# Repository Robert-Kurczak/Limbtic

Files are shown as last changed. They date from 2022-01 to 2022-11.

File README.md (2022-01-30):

# Limbtic
Project Limbtic is an attempt to build a robotic arm that you can control using you own hand. Robotic arm can be bigger, stronger, more precise,
creating many application possibilities.

## Table of Contents
* [General info](#general-info)
* [Hardware](#hardware)

## General info
This project is currently more hardware focused, as I am working on circuit that can handle reading a lot of analog sensors, transform reading into binary form and
send it further so the data can be appropriately proccesed. This circuit have to be fast, precise and noise-resistant.
This kind of circuit have potential on its own as it can be used for example as VR hand controller.

## Hardware
### Sensor Reader
##### Schematic
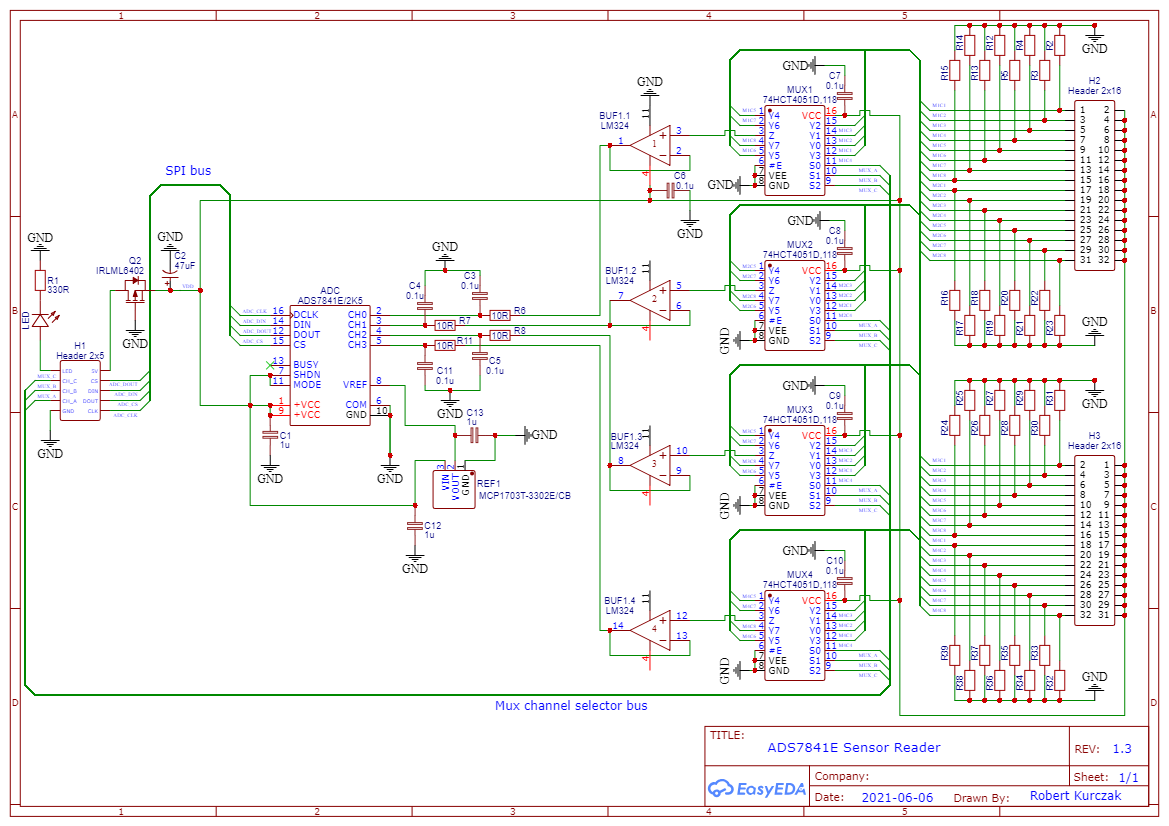
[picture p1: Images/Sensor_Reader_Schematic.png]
Sensor Reader Schematic

##### PCB project
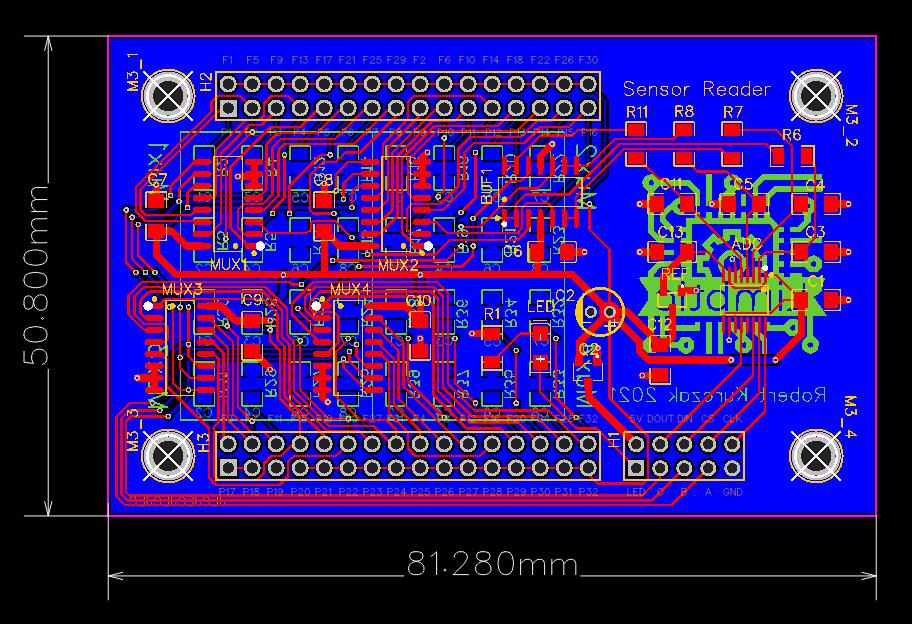
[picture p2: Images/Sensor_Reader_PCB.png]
Sensor Reader PCB project

##### Real photo
Sensor Reader Photo

#### How does it work?
I want to read arm joints angles using some flexible pressure sensors as they're far cheaper than bend sensors, and can be cut to different sizes.
The more you bend sensor, the lesser resistance it have. Using array of resistors on board I create voltage dividers so I can convert resistance to voltage.
After buffering signal to lower impedance, I use low-pass filters to cut off noise above 160kHz. That prepared signal is being read and coverted to binary form by
ADS7841E analog to digital converter and sent futher, for exeample to arduino board, by SPI communication.

### Sensor Reader Connector
##### Schematic
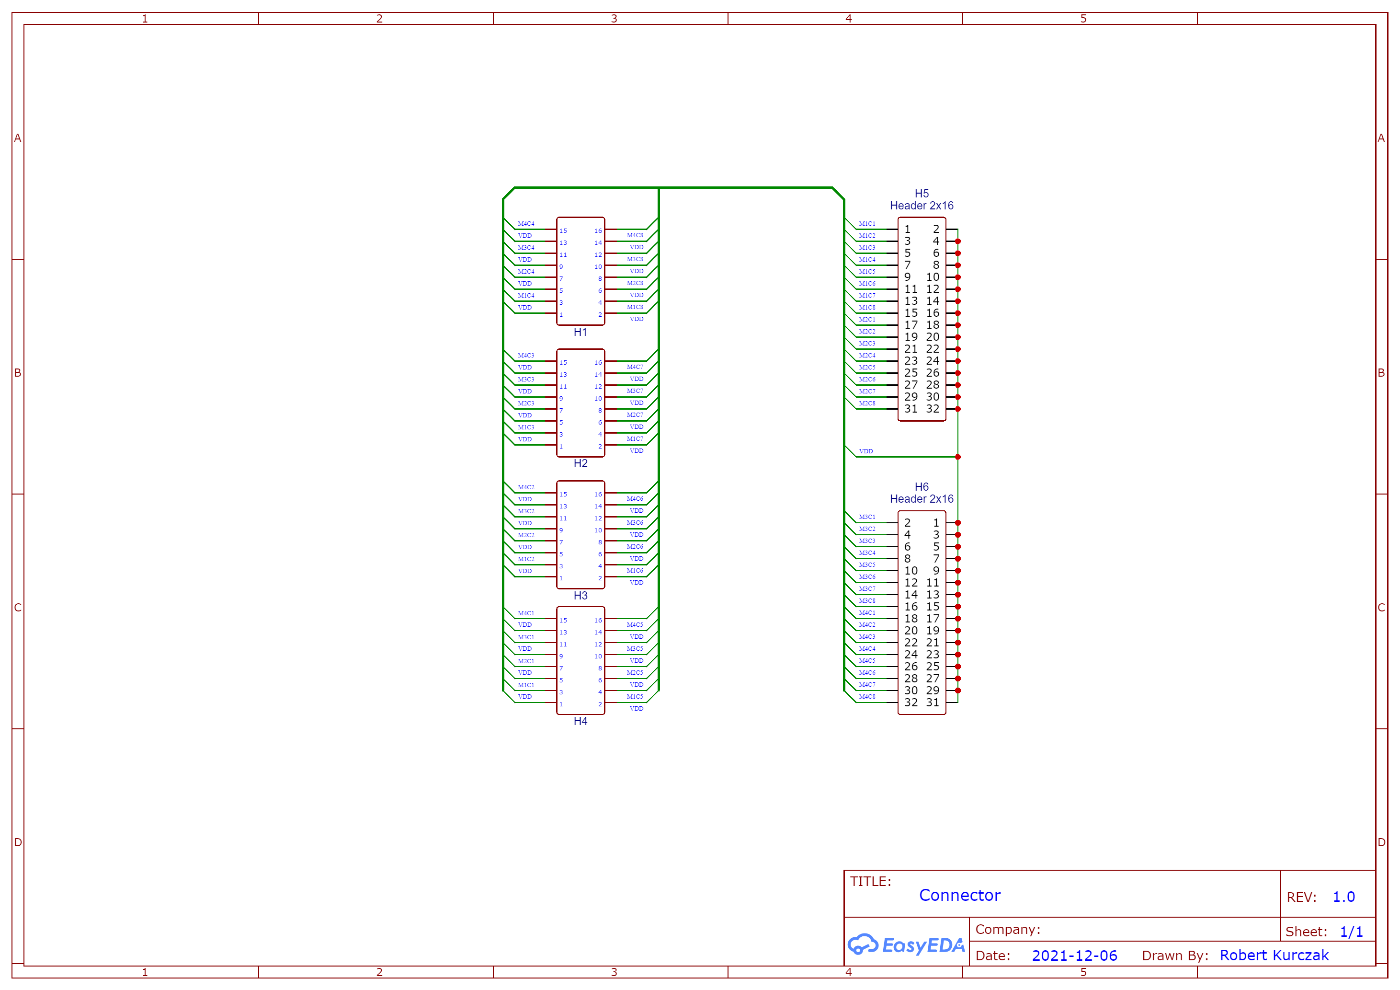
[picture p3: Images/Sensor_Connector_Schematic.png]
Sensor Reader Connector Schematic

##### PCB project
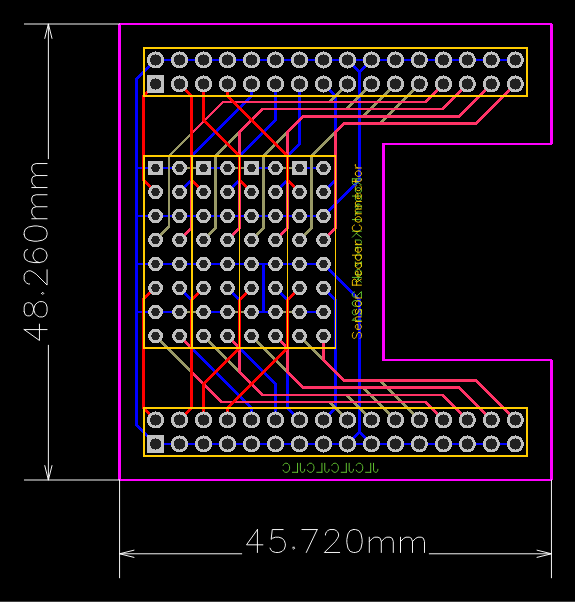
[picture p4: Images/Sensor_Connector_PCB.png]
Sensor Reader Connector PCB project

##### Real photo
Sensor Reader Connector Photo

#### How does it work?
Due to the spacing issues on Sensor Reader board I created little connector that goes on top of it.
It makes sensor connectors be in correct order, from left to right. It also makes connection with main board more solid, as instead of using 2 pin connectors for each sensor,
I can directly solder sensor wires to the header.

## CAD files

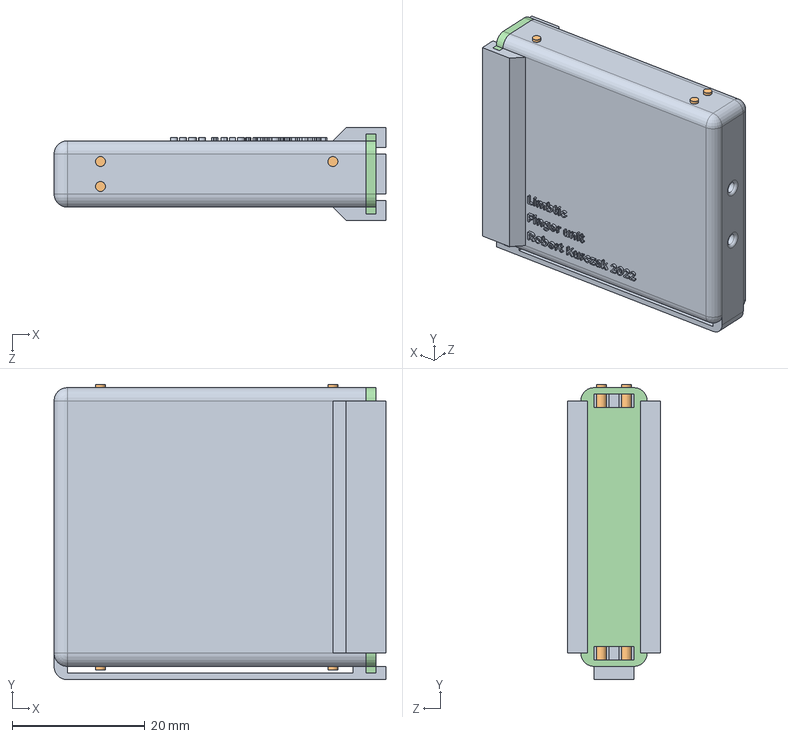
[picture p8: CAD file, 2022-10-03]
3D models/Workspace.SLDASM
50.0 x 44.5 x 14.0 mm
FingerUnit
Potentiometer x 2
Head x 2
FingerUnit-Backcover

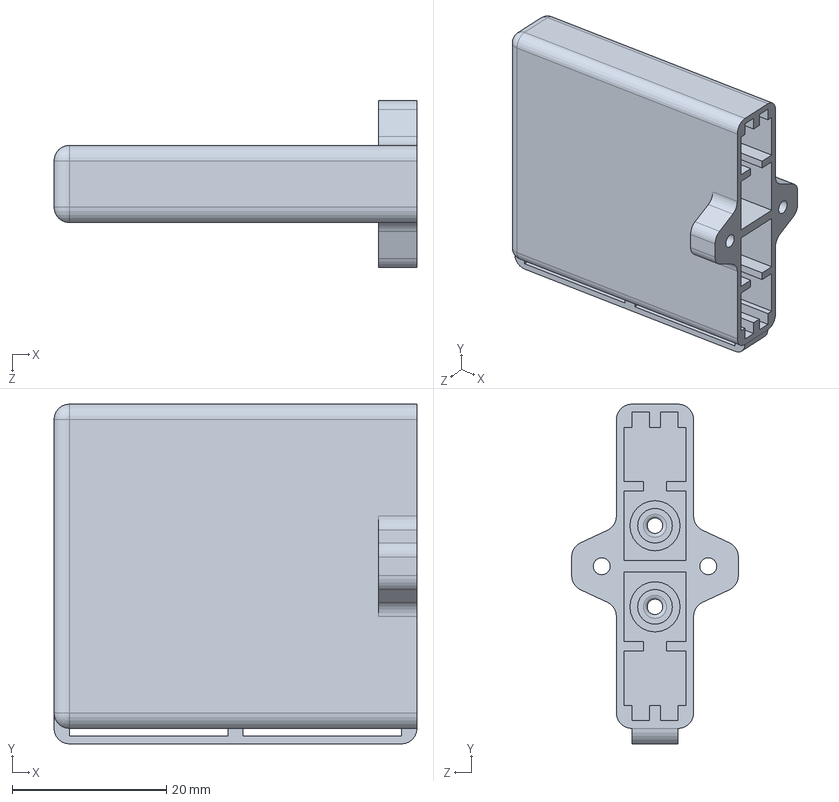
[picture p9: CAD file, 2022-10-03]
3D models/FingerUnit_2.SLDPRT
47.0 x 44.0 x 21.6 mm

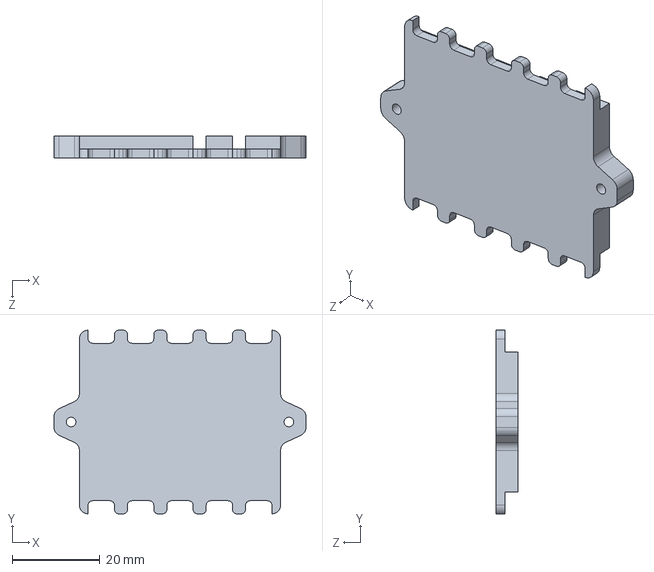
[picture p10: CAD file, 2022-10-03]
3D models/PalmUnit-Backcover.SLDPRT
57.6 x 42.0 x 5.00 mm

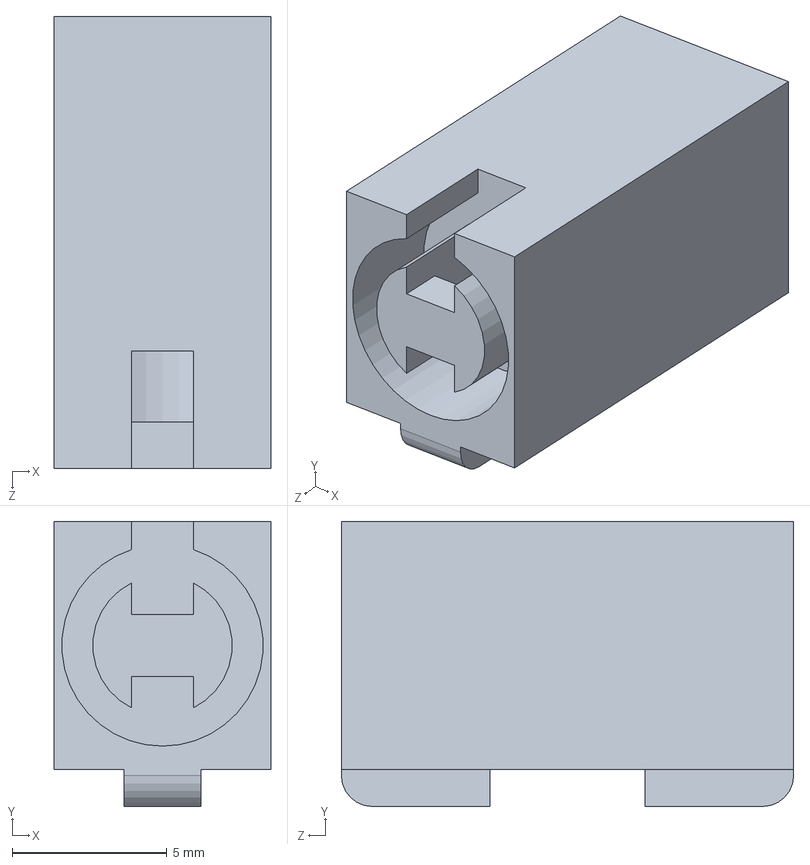
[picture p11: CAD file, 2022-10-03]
3D models/Head.SLDPRT
7.00 x 9.20 x 14.6 mm

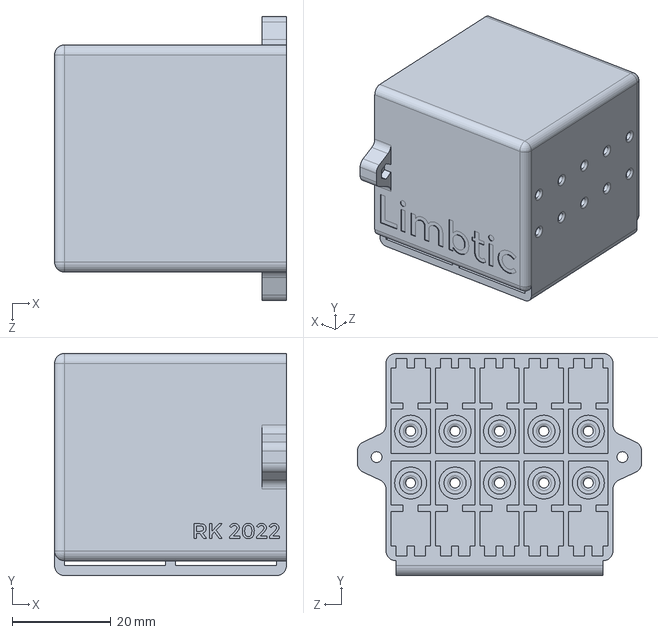
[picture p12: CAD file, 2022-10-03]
3D models/PalmUnit_backup.SLDPRT
47.0 x 45.0 x 57.6 mm

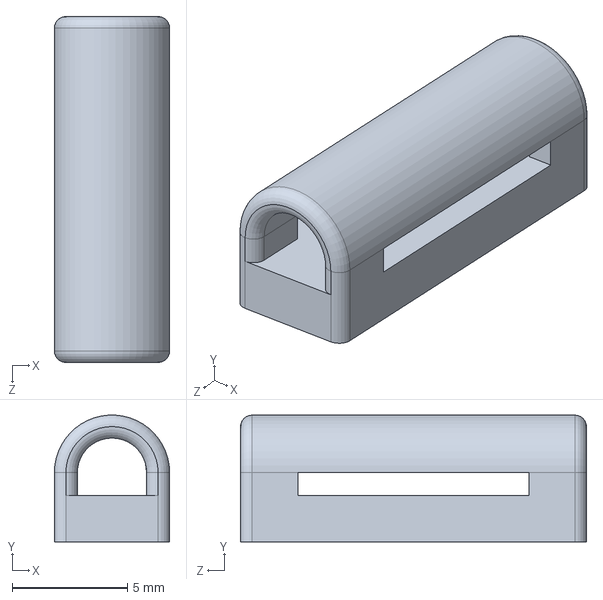
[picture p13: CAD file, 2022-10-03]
3D models/WireGuide.SLDPRT
5.00 x 5.50 x 15.0 mm

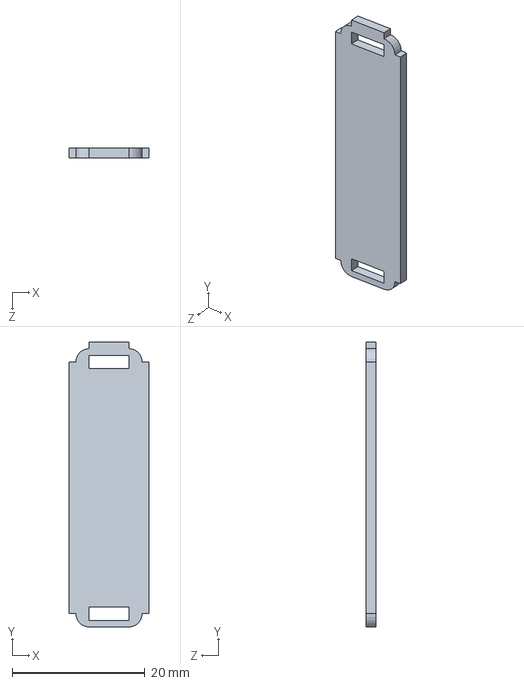
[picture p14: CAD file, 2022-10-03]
3D models/FingerUnit-Backcover.SLDPRT
12.0 x 43.0 x 1.50 mm

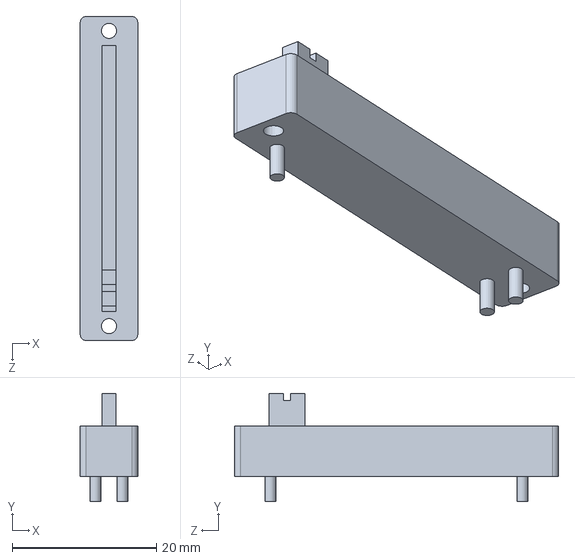
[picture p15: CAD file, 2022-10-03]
3D models/Potentiometer.SLDPRT
8.00 x 15.0 x 45.0 mm

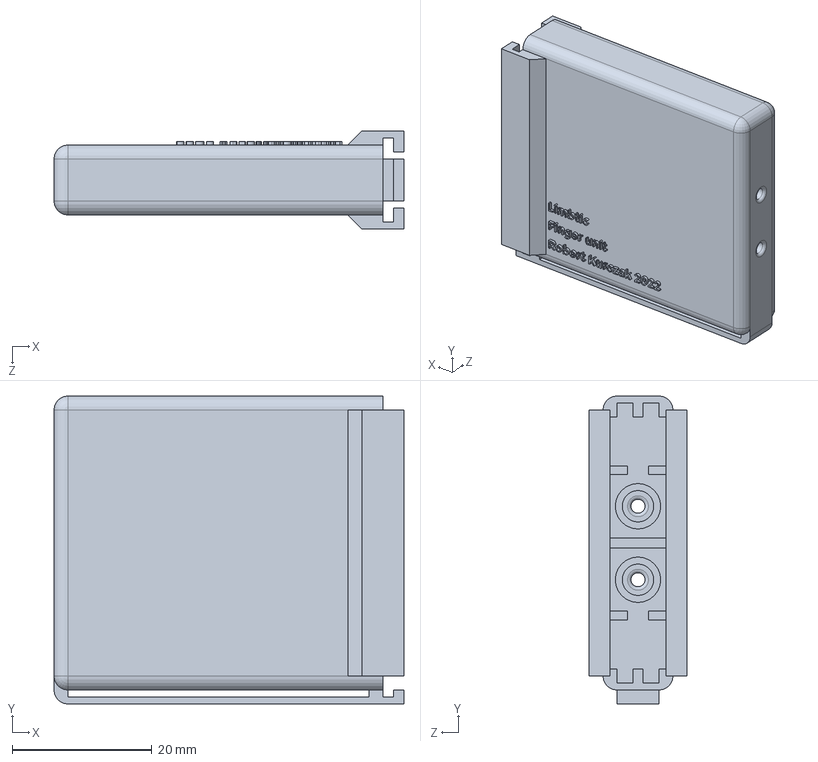
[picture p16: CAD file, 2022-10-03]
3D models/FingerUnit.SLDPRT
50.0 x 44.0 x 14.0 mm

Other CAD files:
3D models/PalmUnit.SLDPRT
3D models/Head_2.SLDPRT
3D models/STLs/FingerUnit-Backcover.STL
3D models/STLs/FingerUnit.STL
3D models/STLs/FingerUnit_2.STL
3D models/STLs/Head.STL
3D models/STLs/Head_2.STL
3D models/STLs/PalmUnit-Backcover.STL
3D models/STLs/PalmUnit.STL
3D models/STLs/WireGuide.STL
Limbtic_Vi/Assets/Fps Arms Pack [Updated] FBX/Arms/No Sleeve/Arm.blend

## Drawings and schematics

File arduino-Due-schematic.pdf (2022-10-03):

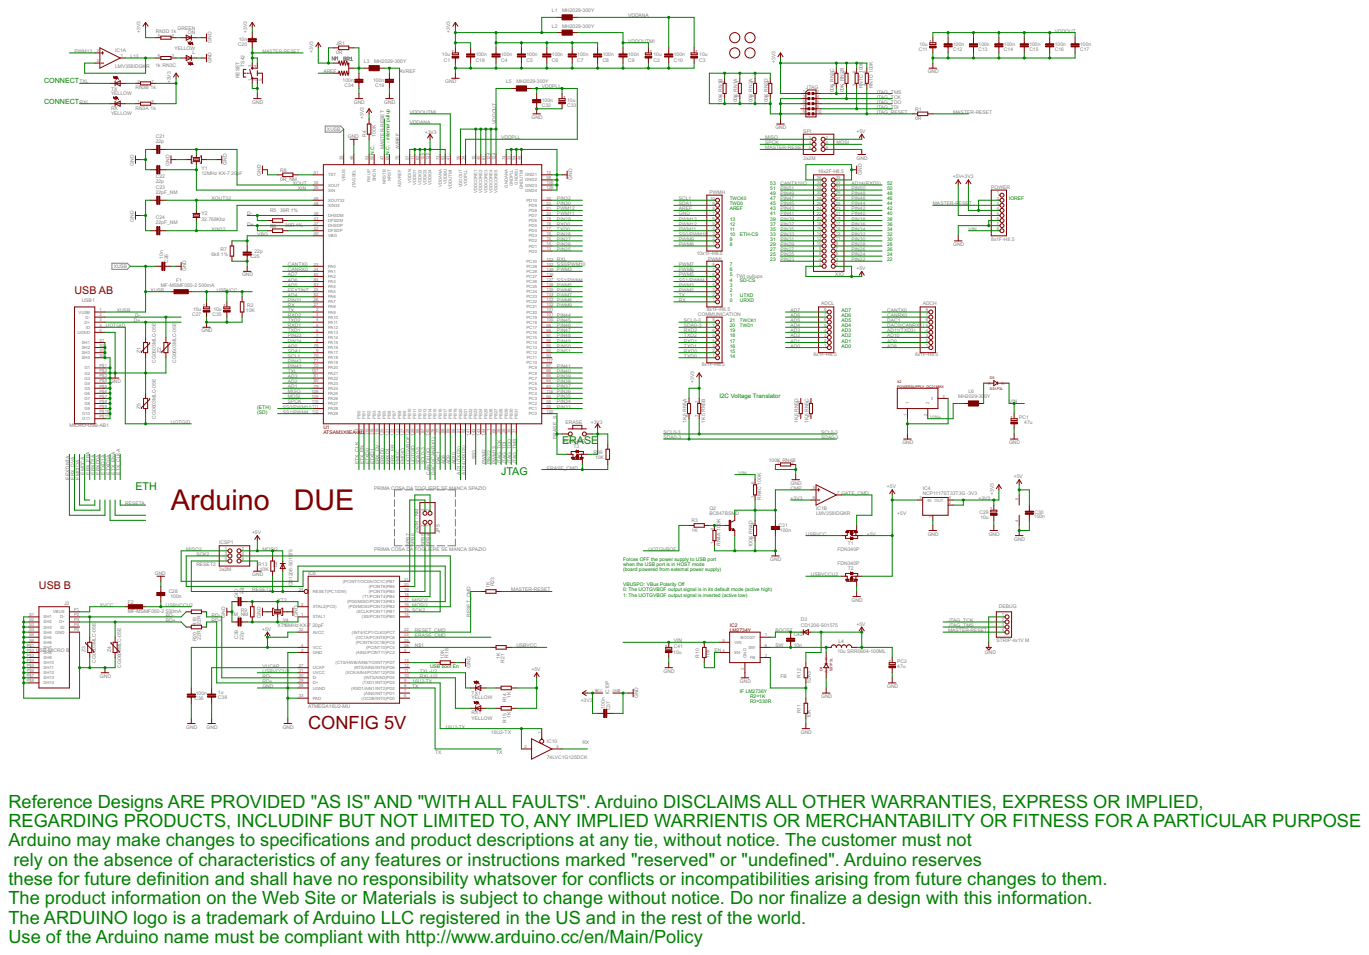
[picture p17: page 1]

PRIMA COSA DA TOGLIERE SE MANCA SPAZIO

SCK2 | 3 4

Forces OFF the power supply to USB port when the USB port is in HOST mode

(board powered from external power supply)

VBUSPO: VBus Polarity Off
0: The UOTGVBOF output signal is in its default mode (active high)
1: The UOTGVBOF output signal is inverted (active low)

Reference Designs ARE PROVIDED "AS IS" AND "WITH ALL FAULTS". Arduino DISCLAIMS ALL OTHER WARRANTIES, EXPRESS OR IMPLIED,
REGARDING PRODUCTS, INCLUDINF BUT NOT LIMITED TO, ANY IMPLIED WARRIENTIS OR MERCHANTABILITY OR FITNESS FOR A PARTICULAR PURPOSE
Arduino may make changes to specifications and product descriptions at any tie, without notice. The customer must not
rely on the absence of characteristics of any features or instructions marked "reserved" or "undefined". Arduino reserves
these for future definition and shall have no responsibility whatsover for conflicts or incompatibilities arising from future changes to them. The product information on the Web Site or Materials is subject to change without notice. Do nor finalize a design with this information. The ARDUINO logo is a trademark of Arduino LLC registered in the US and in the rest of the world. Use of the Arduino name must be compliant with http://www.arduino.cc/en/Main/Policy

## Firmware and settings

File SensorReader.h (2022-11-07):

#include <SPI.h>

//D53
#define CS_PORT_DIR DDRB
#define CS_PORT_STATE PORTB
#define CS_PIN 0

//D46
#define LED_PORT_DIR DDRL
#define LED_PORT_STATE PORTL
#define LED_PIN 3

//CH_A = L0
//CH_B = L1
//CH_C = L2
#define MUX_CH_PORTS_DIR DDRL
#define MUX_CH_PORTS_STATE PORTL


class sensorReader{
    private:
        
        struct sensor{
            char mux;
            char channel;

            sensor(char mux, char channel) : mux(mux), channel(channel){}
        };

        sensor sensorsArray[10] = {
            sensor(1, 1),
            sensor(0, 4),

            sensor(0, 1),
            sensor(3, 0),

            sensor(3, 4),
            sensor(2, 0),

            sensor(2, 4),
            sensor(1, 0),

            sensor(1, 4),
            sensor(0, 0)
        };

        //Channel from 0 to 3
        int readADC(char channel){
            //CS low
            CS_PORT_STATE &= ~byte(1 << CS_PIN);

            byte channelBytes[4] = {0b10010100, 0b11010100, 0b10100100, 0b11100100};

            //---Transfer---
            //Start byte
            SPI.transfer(channelBytes[channel]);

            //Don't care bytes for retriving data
            byte dataP1 = SPI.transfer(0b00000000);
            byte dataP2 = SPI.transfer(0b00000000);

            //CS high
            CS_PORT_STATE |= byte(1 << CS_PIN);
            //------

            //---Data processing---
            int resultInt = dataP1;
            resultInt = resultInt << 8;
            resultInt = resultInt | dataP2;
            resultInt = resultInt >> 3;
            //------

            return resultInt;
        }

        void setMuxChannel(int channel){
                MUX_CH_PORTS_STATE &= 0b00000000;
                MUX_CH_PORTS_STATE |= channel;

                delay(5); //propagation time
        }


    public:
        sensorReader(){
            //Setting mux channel selectors as output
            MUX_CH_PORTS_DIR |= 0b00000111;

            //Setting ADC CS pin as output
            CS_PORT_DIR |= byte(1 << CS_PIN);

            //Setting ADC CS pin high be default (not listening)
            CS_PORT_STATE |= byte(1 << CS_PIN);
        }

        String getDataPackage(){
            String package = "";

            for(int i = 0; i < 10; i++){
                setMuxChannel(sensorsArray[i].channel);

                package += String(readADC(sensorsArray[i].mux));
                package += ";";
            }

            package.remove(package.length() - 1);
            return package;
        }
};

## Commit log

2022-08-15 working sensors reading prototype
2022-09-02 Added 3d models and logos
    [FingerUnit-Backcover.SLDPRT, FingerUnit.SLDPRT, Head.SLDPRT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]
2022-10-03 new STLs
    [FingerUnit-Backcover.SLDPRT, FingerUnit-Backcover.STL, FingerUnit.SLDPRT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]
2022-11-06 fixed mux channels propagation time
    [SensorReader.h]
2022-11-06 added gerber file
2022-11-07 working VI
    [Arm.blend]
